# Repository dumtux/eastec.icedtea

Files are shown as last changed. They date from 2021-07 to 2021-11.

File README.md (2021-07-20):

# IcedTEA - Turntable motor control PCB design

## Overview

Design and prototype a PCB that will accurately control the rotation speed a turntable via pulley. The
board will be connected to a motor with self-encoding and will monitor and adjust the speed of the
motor to ensure target speed is maintained.

## Features

* DC power management
* Onboard microchip for firmware
* Target speed switch (33.33rpm or 45 rpm)
* Display of current & target speed (via OLED or 8 segment display)
* Fine adjustment of target speed +/- 10% via pot
* USB C for power & firmware upgrade
* Motor control and sensing
* Auto adjustment to ensure target speed is achieved
* Motor overload cutout and warning

## References

* [MSP430G2x53 datasheet](https://www.ti.com/lit/ds/symlink/msp430g2553.pdf)
* [OLED Graphic Display Interfacing with MSP -EXP430G2 TI Launchpad](https://www.electronicwings.com/ti-launchpad/oled-graphic-display-interfacing-with-msp-exp430g2-ti-launchpad)

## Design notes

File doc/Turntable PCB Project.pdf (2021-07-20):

## Turntable motor control PCB design

### Overview

Design and prototype a PCB that will accurately control the rotation speed a turntable via pulley. The board will be connected to a motor with self-encoding and will monitor and adjust the speed of the motor to ensure target speed is maintained.

### Features:

- DC power management
- Onboard microchip for firmware
- Target speed switch (33.33rpm or 45 rpm)
- Display of current & target speed (via OLED or 8 segment display)
- Fine adjustment of target speed +/- 10% via pot
- USB C for power & firmware upgrade
- Motor control and sensing
- Auto adjustment to ensure target speed is achieved
- Motor overload cutout and warning

### Notes

An example of a motor BL4235I

PCB may need to be in two parts - one for Switches/buttons and display and one for power and motor control.

PCB/s to be designed to fit in cylindrical machined metal machined housing (See example pictures)

Potentiometers and switches are to be high quality and have a good “feel”

300mm Pulley > 40mm Pulley

PCB to be round with max 85mm diameter

### Block Diagram

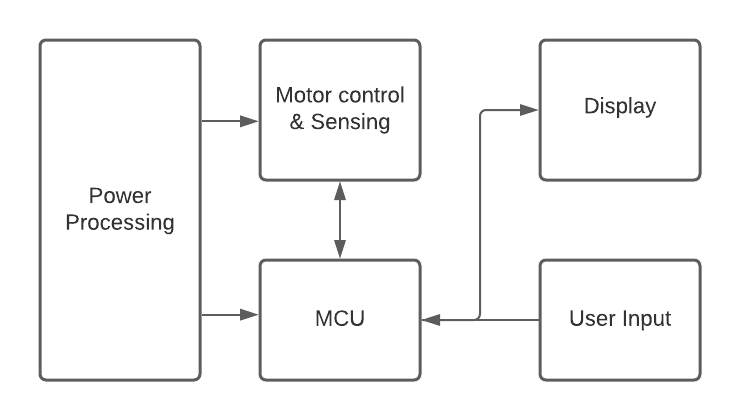
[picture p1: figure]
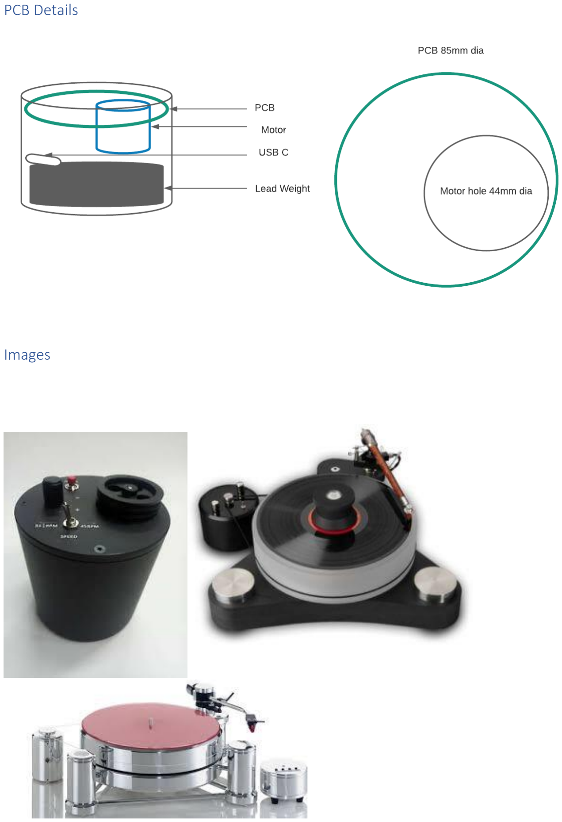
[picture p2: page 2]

### PCB Details

### Images

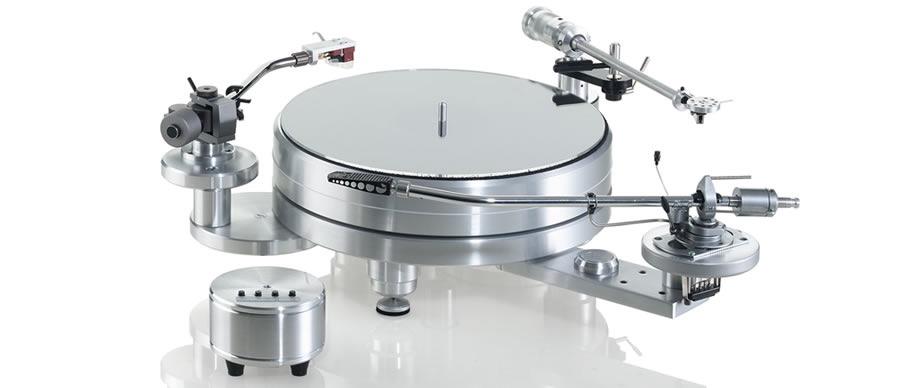
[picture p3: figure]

### Motor Spec

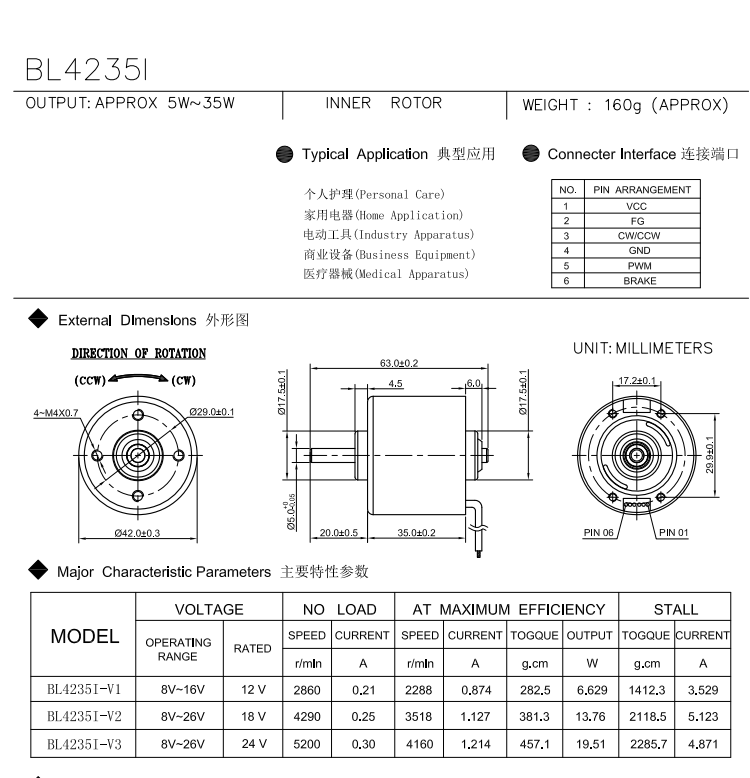
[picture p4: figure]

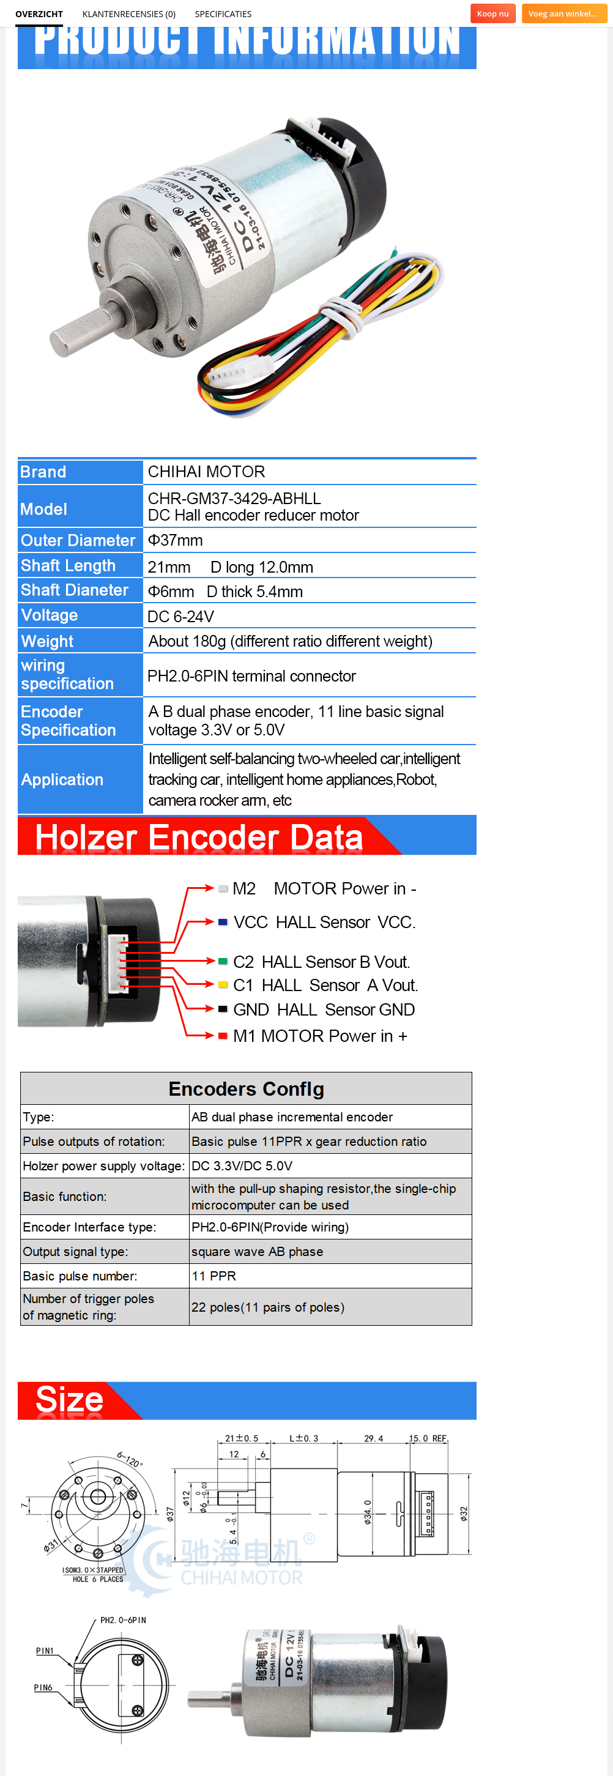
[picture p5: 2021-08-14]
doc/GM37-3429.png

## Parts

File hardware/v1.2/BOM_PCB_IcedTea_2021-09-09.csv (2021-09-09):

ID | Name | Designator | Footprint | Quantity | Manufacturer Part | Manufacturer | Supplier | Supplier Part | Price
1 | EC11G1564411 | SW | SW-TH_EC11M1575403 | 1 | EC11G1564411 | ALPS Electric | LCSC | C470750 | 3.138
2 | 470uF | C20 | CAP-SMD_BD6.3-L6.6-W6.6-FD | 1 | CS0J471M-CRE77 | SEMTECH | LCSC | C114446 | 0.046
3 | 220uF | C3,C6 | CAP-SMD_BD8.0-L8.3-W8.3-RD | 2 | CS1V221M-CRF10 | SEMTECH | LCSC | C97814 | 0.072
4 | TYPEC-304-BCP16 | USB1 | USB-C-SMD_TYPEC-304-BCP16 | 1 | TYPEC-304-BCP16 | XUNPU | LCSC | C720629 | 0.088
5 | CH340B | U2 | SOIC-16_L9.9-W3.9-P1.27-LS6.0-BL | 1 | CH340B | WCH | LCSC | C81010 | 1.19
6 | FC-2012HRK-620D | FAULT | LED0805-RD | 1 | FC-2012HRK-620D | NATIONSTAR | LCSC | C84256 | 0.012
7 | 100 | R4 | R0603 | 1 | 0603WAF1000T5E | UniOhm | LCSC | C22775 | 0.001
8 | 100nF | C19,C18,C9,C10,C31 | C0805 | 5 | CC0805KRX7R9BB104 | YAGEO | LCSC | C49678 | 0.006
9 | A2541HWV-4P | OLED | OLED12864 | 1 | A2541HWV-4P | Changjiang Connectors | LCSC | C225501 | 0.074
10 | 10uF | C7,C8,C11 | C1206 | 3 | CL31A106KBHNNNE | SAMSUNG | LCSC | C13585 | 0.039
11 | 47uF | C12 | CAP-SMD_BD5.0-L5.3-W5.3-RD | 1 | CS1C470M-CRD54 | SEMTECH | LCSC | C96178 | 0.027
12 | 10uH | L3 | L1206 | 1 | CMI321609X100KT | FH | LCSC | C1051 | 0.018
13 | 1nF | C13 | C0603 | 1 | CL10B102KB8NNNC | SAMSUNG | LCSC | C1588 | 0.003
14 | 47K | R1 | R0603 | 1 | 0603WAF4702T5E | UniOhm | LCSC | C25819 | 0.001
15 | 10nF | C14,C15,C16,C17 | C0603 | 4 | 0603B103K500NT | FH | LCSC | C57112 | 0.003
16 | AMS1117-3.3 | U3 | SOT-223-3_L6.5-W3.4-P2.30-LS7.0-BR | 1 | AMS1117-3.3 | AMS | LCSC | C6186 | 0.147
17 | XL6019E1 | U4 | TO-263-5_L10.2-W9.9-P1.70-LS14.4-TL | 1 | XL6019E1 | XLSEMI | LCSC | C73018 | 0.908
18 | SS54_C16103 | D2 | SMC_L7.1-W6.2-LS8.1-R-RD | 1 | SS54 | MDD | LCSC | C16103 | 0.196
19 | 220uF | C1,C2 | CAP-SMD_BD6.3-L6.6-W6.6-RD | 2 | RVT1A221M0605 | HONOR | LCSC | C3345 | 0.035
20 | 47uH | L1,L2 | IND-SMD_L10.5-W10.3_SLD10D50 | 2 | SLD10D50S470MTT | Sunltech Tech | LCSC | C216171 | 0.172
21 | 47uF | C4,C5 | CAP-SMD_BD6.3-L6.6-W6.6-FD | 2 | RVE1V470M0605 | ROQANG | LCSC | C131122 | 0.04
22 | 27K | R2 | R0805 | 1 | 0805W8F2702T5E | UniOhm | LCSC | C17593 | 0.002
23 | 2.7K | R3 | R0805 | 1 | 0805W8F2701T5E | UniOhm | LCSC | C17530 | 0.002
24 | DRV8872DDAR | U5 | HSOP-8_L5.0-W4.0-P1.27-LS6.2-BL-EP | 1 | DRV8872DDAR | TI | LCSC | C114179 | 3.215
25 | X2016WR-06B-N0SN | MOTOR | CONN-TH_6P-P2.00_X2016WR-06B-N0SN | 1 | X2016WR-06B-N0SN | XKB Enterprise | LCSC | C388725 | 0.041
26 | USBLC6-4SC6 | D1 | SOT-23-6_L2.9-W1.6-P0.95-LS2.8-BR | 1 | USBLC6-4SC6 | STMicroelectronics | LCSC | C111212 | 0.209
27 | MSP430G2553IPW20 | U1 | TSSOP-20_L6.5-W4.4-P0.65-LS6.4-BL | 1 | MSP430G2553IPW20 | TI | LCSC | C53923 | 2.428

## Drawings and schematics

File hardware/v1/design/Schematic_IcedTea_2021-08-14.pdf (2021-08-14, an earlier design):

# USB_C GND B1

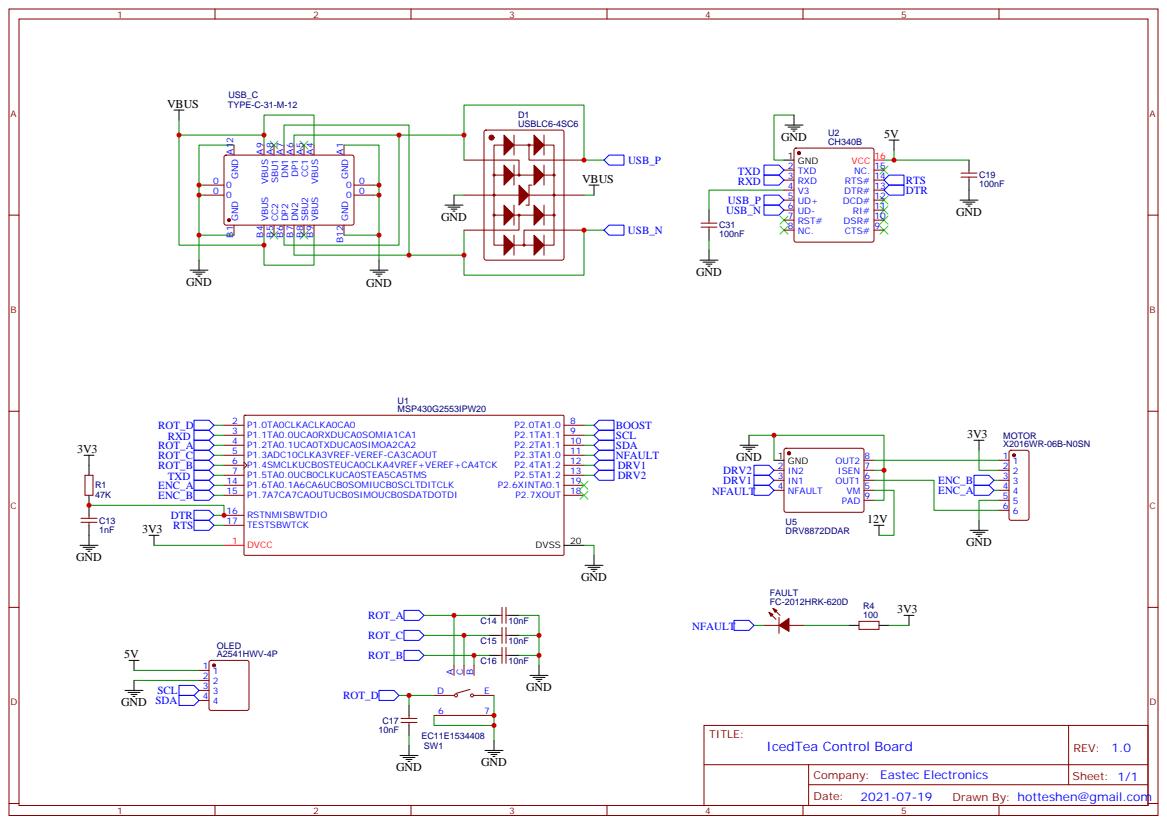
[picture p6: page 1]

DSR# 10 RI# 11 DCD# 12 DTR# 13 RTS# 14 NC. 15 VCC 16

Drawn By: hotteshen@gmail.com

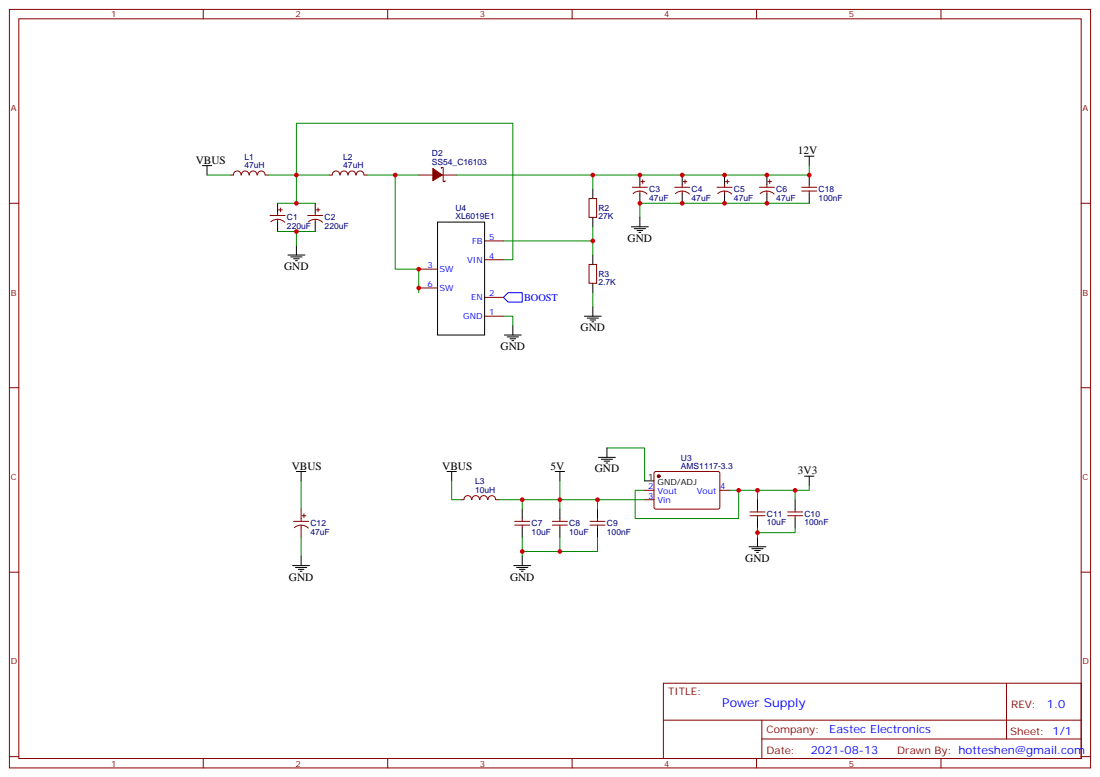
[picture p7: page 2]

Drawn By: hotteshen@gmail.com

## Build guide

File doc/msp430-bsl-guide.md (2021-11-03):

# MSP430 BSL Programming Guide

## Hardware

FT232/CP2102/CH340 | MSP430G2553
-------------------|------------
GND                | GND
VCC (3.3)          | VCC
RX                 | 3
TX                 | 7
RTS                | 17
DTR                | 16

> IMPORTANT: USB-UART converter's TX pin should not wired to 4, RX of MSP430. For BSL, pin 7 (p1.5 SCLK) should be used.

## Software

Install ```mspdebug``` and use,

```sh
sudo apt install mspdebug
mspdebug rom-bsl -d /dev/ttyUSB0 "prog path/to/hexfile"
```

Or use the following script.

```py
#!/usr/bin/env python
# Ref <https://github.com/upsidedownlabs/msptool>

import os
import platform
import argparse

try:
    import serial
except ImportError:
    print("Pyserial is not installed!")
    raise

__version__ = "0.3"

# Argument parsing
help = {"port": "USB-UART bridge port, Windows: COM#, Linux: /dev/tty#",
        "firmware": ".txt(TI-TXT)/.elf/.hex/.bin format firmware image from msp430-gcc/CCS/Energia",
        "directory": "relative msptool directory (if required!)"}
parser = argparse.ArgumentParser()
parser.add_argument('-p', '--port', required=True, type = str, help=help["port"])
parser.add_argument('-f', '--firmware', required=True, type=argparse.FileType('r'), help=help["firmware"])
parser.add_argument('-d', '--directory', required=False, type= str, default=".", help=help["directory"])
args = parser.parse_args()

# Extract info from parsed arguments
comPort = args.port
firmwareImage = args.firmware.name
mspdebugDirectory = args.directory

# Method to Reset connected MSP430
def reset():
    '''Generate reset signal on DTR pin of USB-UART bridge'''
    bridge = serial.Serial(comPort, 9600)
    print("Resetting...")
    bridge.dtr = 0
    bridge.dtr = 1
    bridge.close()

# Get the OS specific command to execute
if platform.system() == 'Windows':
    '''Command for Windows'''
    #command = "rom-bsl.exe -c" + str.upper(comPort) + " -m1 -ievpr " + firmwareImage
    command = mspdebugDirectory + "\mspdebug\mspdebug.exe rom-bsl -d " + str.upper(comPort) + " \"prog " + firmwareImage + "\""
elif platform.system() == 'Linux':
    '''Command for Linux'''
    command = mspdebugDirectory + "/mspdebug/mspdebug rom-bsl -d " + comPort + " \"prog " + firmwareImage + "\""
elif platform.system() == 'Darwin':
    '''Command for OS X'''
    command = mspdebugDirectory + "/mspdebug/mspdebug_osx rom-bsl -d " + comPort + " \"prog " + firmwareImage + "\""
else:
    '''Confused!'''
    print("OS detection ERROR!")
    print("Only Linux/Windows/OSx supported..")

# Print the command
print("msptool v" + __version__)
print("Executing: " + command)
# Execute command
os.system(command)
# Reset chip
reset()
```

---

* Last updated on Nov 3rd, 2021

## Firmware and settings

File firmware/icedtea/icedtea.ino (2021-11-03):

#include <Wire.h>
#include <string.h>

#include "font.h"
#include "images.h"

#define OLED_Write_Address 0x3C

#define ROT_D 2
#define ROT_A 4
#define ROT_B 6
#define ROT_C 5

#define ENC_PIN_A 14
#define ENC_PIN_B 15

#define BOOST  8
#define NFAULT 11
#define DRV_1  12
#define DRV_2  13

#define STEP 1


bool enc_a_raised = false;
bool enc_b_raised = false;

int value = 0;

void rotary_init() {
    pinMode(DRV_1, OUTPUT);
    pinMode(DRV_2, OUTPUT);
    pinMode(BOOST, OUTPUT);

    delay(20);

    digitalWrite(DRV_1, LOW);
    digitalWrite(DRV_2, LOW);
    digitalWrite(BOOST, HIGH);

    delay(20);

    pinMode(ROT_C, OUTPUT);
    digitalWrite(ROT_C, LOW);
    pinMode(ROT_A, INPUT_PULLUP);
    pinMode(ROT_B, INPUT_PULLUP);
    pinMode(ROT_D, INPUT_PULLUP);
    attachInterrupt(ROT_A, ISR_encode_a, CHANGE);
    attachInterrupt(ROT_D, ISR_encode_d, FALLING);
}

void ISR_encode_a(){
    if (digitalRead(ROT_A) == HIGH && digitalRead(ROT_B) == HIGH) {
        decrease_value();
    } else if (digitalRead(ROT_A) == HIGH && digitalRead(ROT_B) == LOW) {
        increase_value();
    } else if (digitalRead(ROT_A) == LOW && digitalRead(ROT_B) == HIGH) {
        increase_value();
    } else if (digitalRead(ROT_A) == LOW && digitalRead(ROT_B) == LOW) {
        decrease_value();
    }
}

void ISR_encode_d(){
    showValue(999);
}

void increase_value() {
    if (value < 256) {
        value += STEP;
    }
   analogWrite(DRV_2, value);
//    showValue(value);
}

void decrease_value() {
    if (value > 0) {
        value -= STEP;
    }
   analogWrite(DRV_2, value);
//    showValue(value);
}

void showValue(int v) {
    char myArray[20]="";
    int z = v;
    for (int i = 2; i>=0; i--) {
        myArray[i] = (z % 10) + 0x30;
        z = z / 10;
    }
    OLED_setXY(0x20, 0x7F, 0x02, 0x01);
    OLED_Data(myArray, 4, 0);
    OLED_setXY(0x20, 0x7F, 0x03, 0x01);
    OLED_Data(myArray, 4, 1);
    OLED_setXY(0x20, 0x7F, 0x04, 0x01);
    OLED_Data(myArray, 4, 2);
    OLED_setXY(0x20, 0x7F, 0x05, 0x01);
    OLED_Data(myArray, 4, 3);
}

void OLED_Data(char *DATA, int m, int n) /* Function for sending data to OLED */
{
    int len = strlen(DATA);
    for (int g=0; g<len; g++)
    {
        for (int index=F32_DLEN/m*n; index<F32_DLEN/m*(n+1); index++)
        {
            Wire.beginTransmission(OLED_Write_Address); /* Begin transmission to slave device */
        /* Queue data to be transmitted */
            Wire.write(0x40); /* For Data Transmission, C = 0 and D/C = 1 */
            Wire.write(F32[DATA[g] - 0x20][index]);
            Wire.endTransmission(); /* Transmit the queued bytes and end transmission to slave device */
        }
    }
}

void OLED_Command(char DATA) /* Function for sending command to OLED */
{
    Wire.beginTransmission(OLED_Write_Address); /* Begin transmission to slave device */
    /* Queue data to be transmitted */
    Wire.write(0x00); /* For Data Transmission, C = 0 and D/C = 0 */
    Wire.write(DATA);
    Wire.endTransmission(); /* Transmit the queued bytes and end transmission to slave device */
}

void OLED_clear(void) /* Function for clearing OLED */
{
    OLED_setXY(0x00, 0x7F, 0x00, 0x07); /* Column Start Address 0, Column End Address 127, Page Start Address 0, Page End Address 7    */
    for (int k=0; k<=1023; k++)
    {
        Wire.beginTransmission(OLED_Write_Address); /* Begin transmission to slave device */
    /* Queue data to be transmitted */
        Wire.write(0x40); /* For Data Transmission, C = 0 and D/C = 1 */
        Wire.write(0x00);
        Wire.endTransmission(); /* Transmit the queued bytes and end transmission to slave device */
    }
}

void OLED_setXY(char col_start, char col_end, char page_start, char page_end) /* Function for setting cursor for writing data */
{
    Wire.beginTransmission(OLED_Write_Address); /* Begin transmission to slave device */
    /* Queue data to be transmitted */
    Wire.write(0x00); /* For Data Transmission, C = 0 and D/C = 0 */
    Wire.write(0x21); /* Set Column Start and End Address */
    Wire.write(col_start); /* Column Start Address col_start */
    Wire.write(col_end); /* Column End Address col_end */
    Wire.write(0x22); /* Set Page Start and End Address */
    Wire.write(page_start); /* Page Start Address page_start */
    Wire.write(page_end); /* Page End Address page_end */
    Wire.endTransmission(); /* Transmit the queued bytes and end transmission to slave device */
}

void OLED_init(void) /* Function for initializing OLED */
{
    OLED_Command(0xAE); /* Entire Display OFF */
    OLED_Command(0xD5); /* Set Display Clock Divide Ratio and Oscillator Frequency */
    OLED_Command(0x80); /* Default Setting for Display Clock Divide Ratio and Oscillator Frequency that is recommended */
    OLED_Command(0xA8); /* Set Multiplex Ratio */
    OLED_Command(0x3F); /* 64 COM lines */
    OLED_Command(0xD3); /* Set display offset */
    OLED_Command(0x00); /* 0 offset */
    OLED_Command(0x40); /* Set first line as the start line of the display */
    OLED_Command(0x8D); /* Charge pump */
    OLED_Command(0x14); /* Enable charge dump during display on */
    OLED_Command(0x20); /* Set memory addressing mode */
    OLED_Command(0x00); /* Horizontal addressing mode */
    OLED_Command(0xA1); /* Set segment remap with column address 127 mapped to segment 0 */
    OLED_Command(0xC8); /* Set com output scan direction, scan from com63 to com 0 */
    OLED_Command(0xDA); /* Set com pins hardware configuration */
    OLED_Command(0x12); /* Alternative com pin configuration, disable com left/right remap */
    OLED_Command(0x81); /* Set contrast control */
    OLED_Command(0x80); /* Set Contrast to 128 */
    OLED_Command(0xD9); /* Set pre-charge period */
    OLED_Command(0xF1); /* Phase 1 period of 15 DCLK, Phase 2 period of 1 DCLK */
    OLED_Command(0xDB); /* Set Vcomh deselect level */
    OLED_Command(0x20); /* Vcomh deselect level ~ 0.77 Vcc */
    OLED_Command(0xA4); /* Entire display ON, resume to RAM content display */
    OLED_Command(0xA6); /* Set Display in Normal Mode, 1 = ON, 0 = OFF */
    OLED_Command(0x2E); /* Deactivate scroll */
    OLED_Command(0xAF); /* Display on in normal mode */
}

void setup() {
    Wire.begin(); /* Initiate wire library and join I2C bus as a master */
    OLED_init(); /* Initialize OLED */

    delay(100);
    OLED_clear(); /* Clear OLED */
    delay(100);

    rotary_init();
}

void loop() {
  showValue(value);
  delay(1000);
}

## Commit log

2021-08-09 add rotary motor control spike.
2021-08-14 hardware design v1.
    [BOM_PCB_IcedTea_2021-08-14.csv, PCB_IcedTea_2021-08-14.pcbdoc, PickAndPlace_PCB_IcedTea_2021-08-14.csv]
2021-08-14 top cover pcb design.
2021-08-14 add motor tech data.
2021-09-09 add hardware v1.2 design files.
    [BOM_PCB_IcedTea_2021-09-09.csv, PickAndPlace_PCB_IcedTea_2021-09-09.csv]
